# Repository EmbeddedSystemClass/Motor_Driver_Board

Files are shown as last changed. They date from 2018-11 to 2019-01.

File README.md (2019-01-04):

# ZJUNlict Motor Driver Board

The motor driver board is used to drive the motor and report the over current signal to the [mother board](https://github.com/ZJUNlict/Mother_Board). (The board is designed using [Altium Designer](https://www.altium.com/altium-designer/) 17.1)

We use half-bridge driver shown in the figure below for BLDC motors. 

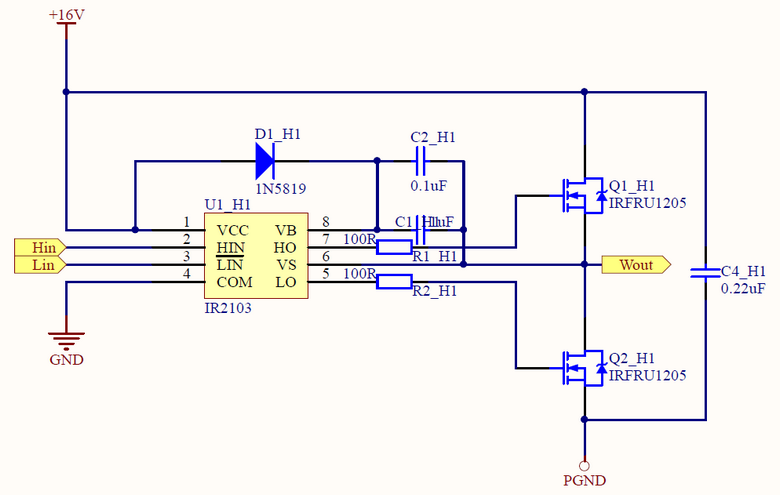
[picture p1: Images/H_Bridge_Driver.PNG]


The main features are:

* Use half-bridge driver(IR2103) to drive MOSFETs(IRFR1205) with internal set deadtime to reduce the complex of core board driver algorithm.
* Current sensor(ACS712) measures the current draw of each motor. Then the comparator(LM339) compares the output voltage signal with reference voltage to detect overcurrent scenarios.
* Motor driver boards uses modular design. One Half-bridge module handles one motor for easier fault identification and quick replacement.

The photos of the motor driver board are shown below as references. 

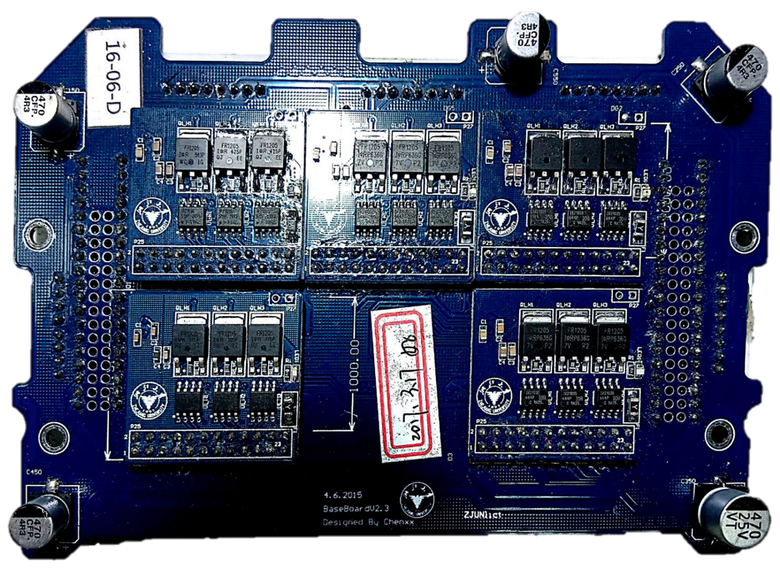
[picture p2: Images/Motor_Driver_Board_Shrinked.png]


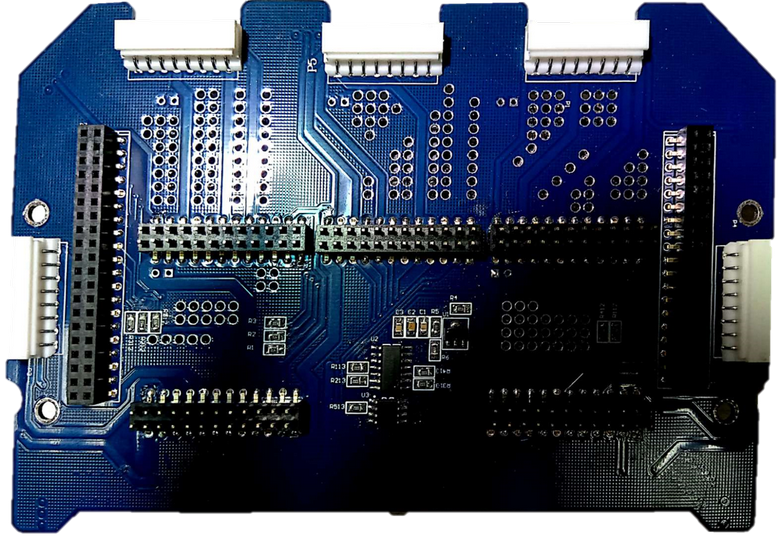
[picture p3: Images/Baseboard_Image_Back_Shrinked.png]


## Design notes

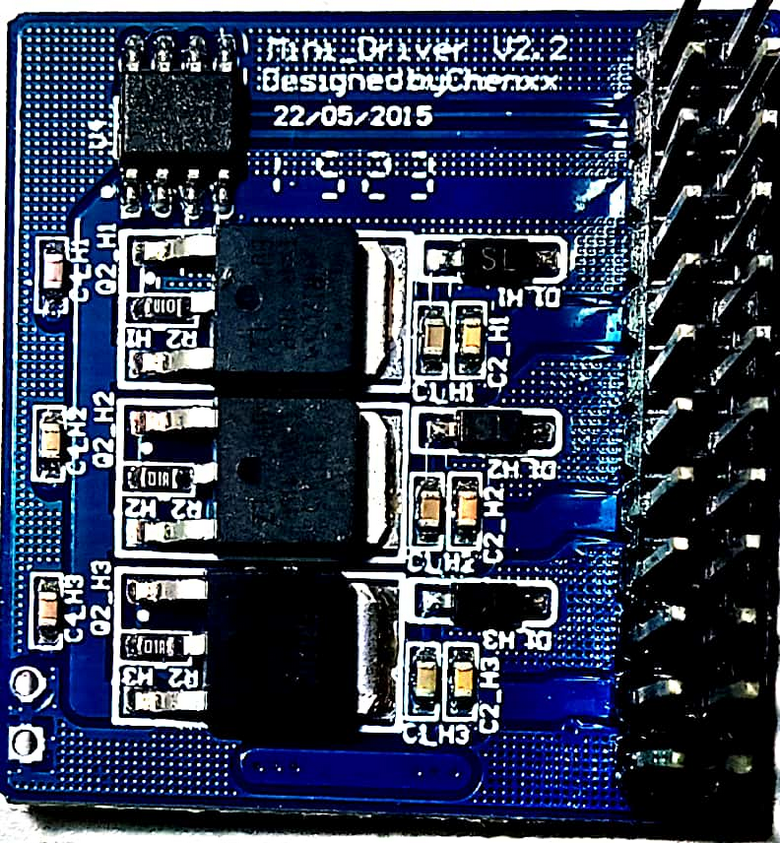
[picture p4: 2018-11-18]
Images/HBridge_Image_Back_Shrinked.png

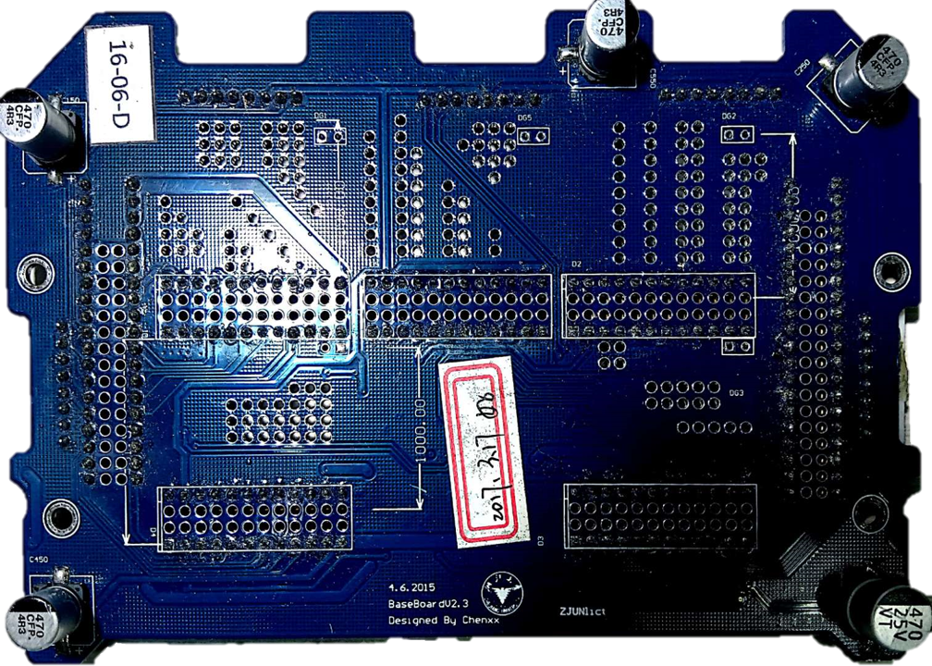
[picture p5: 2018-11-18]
Images/Baseboard_Image_Front.png

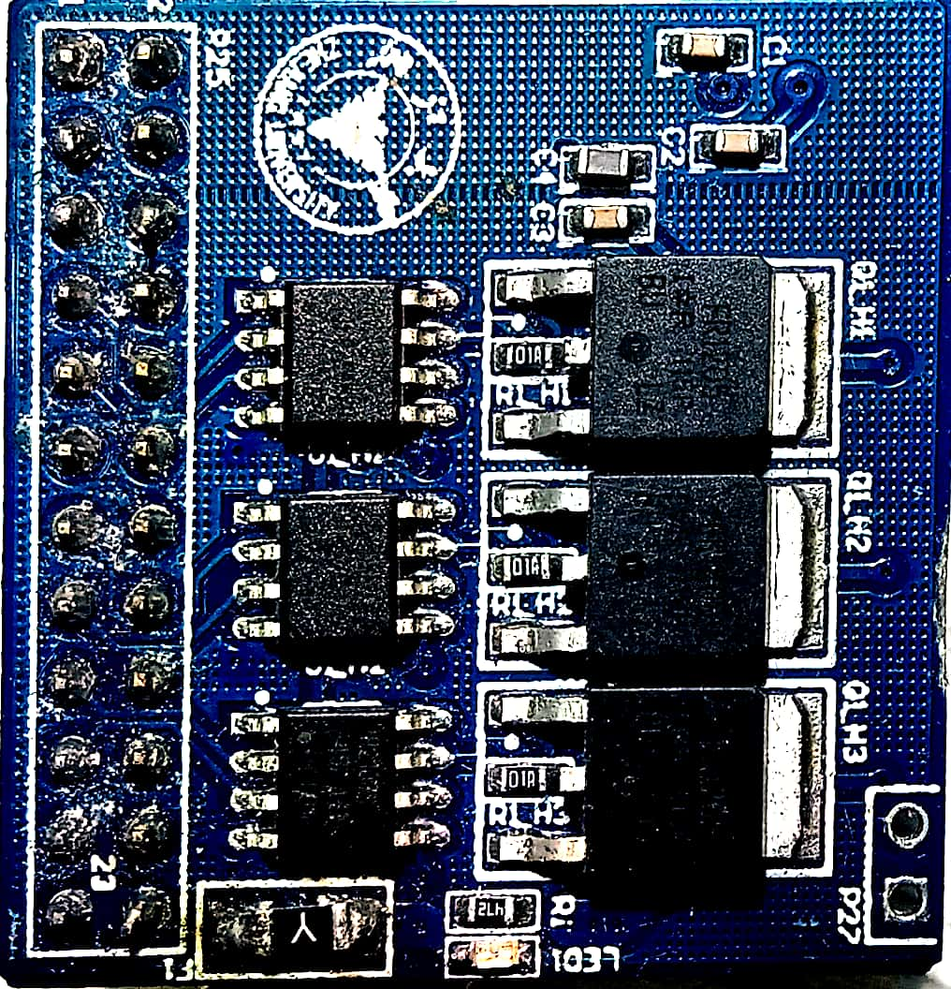
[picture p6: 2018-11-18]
Images/HBridge_Image_Front.png

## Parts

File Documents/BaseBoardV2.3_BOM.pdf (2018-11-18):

Comment | Description | Designator | Footprint | LibRef | Quantity
0.1uF | | C1, C3 | 0805 | cap | 2
1uF | | C2 | 0805 | cap | 1
470uF | 470uF | C150, C250, C350, C450, C550 | Cap - duplicate1 | cap-pol | 5
header-12X2 | | D1, D2, D3, D4, D5 | Header-12X2-wgj | NDK-22P | 5
Header 2 | | DG1, DG2, DG3, DG4, DG5 | HDR1X2 | header-2P | 5
BNC | BNC Elbow Connector | H1, H2, H3, H4 | BNC | BNC | 4
Header_8P | Header, 8-Pin | P1, P2, P3, P4, P5 | Header_8P | Header 8 | 5
Header_19*2P | Header, 19-Pin, Dual row | P6 | Header_19*2P | Header 19X2 | 1
Header_20*2P | | P7 | Header_20*2P | Header_20*2P | 1
4.7K | | R1, R2, R3 | 0805 | res | 3
470 | | R4 | 0805 | res | 1
1.6k | | R5 | 0805 | res | 1
22k | | R6 | 0805 | res | 1
10K | | R112, R113, R212, R213, R312, R313, R412, R413, R512, R513 | 0805 | res | 10
TL431CLP | | U1 | SOT89 | TL431CLP | 1
LM339 | | U2 | SOP14 | LM339 | 1
LM393 | | U3 | LM393 | LM393 | 1

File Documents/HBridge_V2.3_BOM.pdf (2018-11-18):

Bill of Materials | Bill of Materials For PCB Document [HBridge_V2.3.PcbDoc]
Source Data From: | HBridge_V2.3.PcbDoc
Project: | | H-Bridge-SingleV2.2.PrjPCB
Variant: | | None
Creation Date: 2015/6/4 | 22:10:00
Print Date: | 43422 | 43422.83022
Footprint | Comment | LibRef | Designator | Description | Quantity
0603 | 1nF | cap | C1 | | 1
0603 | 1uF | cap | C1_H1, C1_H2, C1_H3 | | 3
0603 | 0.1uF | cap | C2, C2_H1, C2_H2, C2_H3, C3 | | 5
0603 | 10uF | cap | C4 | | 1
0603 | 0.22uF | cap | C4_H1, C4_H2, C4_H3 | | 3
SOD-123 | 1N5819 | diode | D1_H1, D1_H2, D1_H3 | | 3
FUSE | 5A | FUSE | F1 | | 1
0603_diode | green | led | LED1 | | 1
HDR2X12 | Header 12X2 | Header 12X2 | P25 | Header, 12-Pin, Dual row | 1
HDR1X2 | Header 2 | Header 2 | P27 | Header, 2-Pin | 1
TO-252 | IRFRU1205 | IRFRU1205 | Q1_H1, Q1_H2, Q1_H3, Q2_H1, Q2_H2, Q2_H3 | | 6
0603 | 4.7k | res | R1 | | 1
0603 | 100R | res | R1_H1, R1_H2, R1_H3, R2_H1, R2_H2, R2_H3 | | 6
SOIC-8 | IR2103 | IR2103 | U1_H1, U1_H2, U1_H3 | | 3
SOIC-8 | ACS712 | ACS712 | U4 | | 1
| | | | | 37
Approved | | Notes
Altium Limited Confidential | 2018/11/18 | Page 1

### Project Full Path Project Filename Variant Name Data-Source Filename Data-Source Full Path Title Total Quantity Report Time Report Date Report Date & Tine Output Name Output Type Output Generator Name Output Generator Description

D:\Engneering\electronics\project\ZJUNlict_Brushless\HBridge-V2.2\H-Bridge-SingleV2.2.PrjPCB H-Bridge-SingleV2.2.PrjPCB
None
HBridge_V2.3.PcbDoc
D:\Engneering\electronics\project\ZJUNlict_Brushless\HBridge-V2.2\HBridge_V2.3.PcbDoc Bill of Materials For PCB Document [HBridge_V2.3.PcbDoc]
37
22:10:00
2015/6/4
2015/6/4 22:10:00
Bill of Materials
BOM_PartType
BOM
Bill of Materials

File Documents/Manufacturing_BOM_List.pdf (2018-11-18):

Comment | Description | Designator | Footprint | LibRef | Quantity | Company
0.1uF | ±10%,50V,-55to+125℃ | C1, C3 | 0805 | cap | 2
1uF | ±10%,50V,-55to+125℃ | C2 | 0805 | cap | 1
470uF | ±10%,25V,10*10mm,-55°C to +125°C | C150, C250, C350, C450, C550 | Cap - duplicate1 | cap-pol | 5
header-12X2 | 205-2X12P-7.62 | D1, D2, D3, D4, D5 | Header-12X2-wgj | SHPEAK | 5 SHPEAK
Header 2 | 201S-1X2PG-10.0/3.0 | DG1, DG2, DG3, DG4, DG5 | HDR1X2 | | 5
BNC | | H1, H2, H3, H4 | BNC | BNC | 4
Header_8P | 5264-8AW / 22-05-7085 | P1, P2, P3, P4, P5 | Header_8P | Header 8 | 5 MOLEX
Header_19*2P | 205-2X10P-7.62 | P6 | Header_19*2P | SHPEAK | 2 SHPEAK
Header_20*2P | 205-2X10P-7.62 | P7 | Header_20*2P | SHPEAK | 2 SHPEAK
4.7K | 0.01 R1, R2, R3 | | 0805 | res | 3
470 | 0.01 R4 | | 0805 | res | 1
1.6k | 0.01 R5 | | 0805 | res | 1
22k | 0.01 R6 | | 0805 | res | 1
10K | 0.01 R112, R113, R212, R213, R312, R313, R412, R413, R512, R513 | | 0805 | res | 10
TL431CLP | | U1 | SOT89 | TL431CLP | 1 TI
LM339 | | U2 | SOP14 | LM339 | 1 TI
LM393 | | U3 | LM393 | LM393 | 1 TI

Footprint | Comment | LibRef | Designator | Company | Description | Quantity
0603 | 1nF | cap | C1 | | ±10%，50V，-55to+125℃ | 1
0603 | 1uF | cap | C1_H1, C1_H2, C1_H3 | | ±10%，50V，-55to+125℃ | 3
0603 | 0.1uF | cap | C2, C2_H1, C2_H2, | | ±10%，50V，-55to+125℃ | 5
0603 | 10uF | cap | C4 | | ±10%，50V，-55to+125℃ | 1
0603 | 0.22uF | cap | C4_H1, C4_H2, C4_H3 | | ±10%，50V，-55to+125℃ | 3
SOD-123 | 1N5819 | DIODE | D1_H1, D1_H2, D1_H3 | DIODESINC. | | 3
1206 | 5A | FUSE | F1 | BOURNS | SF-1206S50 Slow Blow | 1
0603_diode | GREEN | LED | LED1 | | | 1
HDR2X12 | Header 2X12 | Header 12X2 | P25 | | | 1
HDR1X2 | Header 2 | Header 2 | P27 | | | 1
TO-252 | IRFRU1205 | IRFRU1205 | Q1_H1, Q1_H2, Q1_H3, Q2_H1, Q2_H2, Q2_H3 | INTERNATIONA L RECTIFIER | | 6
0603 | 4.7k | res | R1 | | 1% | 1
0603 | 100R | res | R1_H1, R1_H2, R1_H3, R2_H1, R2_H2, R2_H3 | | 1% | 6
SOIC-8 | IR2103 | IR2103 | U1_H1, U1_H2, U1_H3 | INTERNATIONA L RECTIFIER | | 3
SOIC-8 | ACS712 | ACS712 | U4 | ALLEGRO MICROSYSTEM S | | 1

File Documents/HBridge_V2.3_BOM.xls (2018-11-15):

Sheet: BOM Report
Bill of Materials |  |  | Bill of Materials For PCB Document [HBridge_V2.3.PcbDoc]
Source Data From: |  | HBridge_V2.3.PcbDoc
Project: |  | H-Bridge-SingleV2.2.PrjPCB
Variant: |  | None
Creation Date: | 2015/6/4 | 22:10:00
Print Date: | 42159 | 42159.92383
Footprint | Comment | LibRef | Designator | Description | Quantity
0603 | 1nF | cap | C1 |  | 1
0603 | 1uF | cap | C1_H1, C1_H2, C1_H3 |  | 3
0603 | 0.1uF | cap | C2, C2_H1, C2_H2, C2_H3, C3 |  | 5
0603 | 10uF | cap | C4 |  | 1
0603 | 0.22uF | cap | C4_H1, C4_H2, C4_H3 |  | 3
SOD-123 | 1N5819 | diode | D1_H1, D1_H2, D1_H3 |  | 3
FUSE | 5A | FUSE | F1 |  | 1
0603_diode | green | led | LED1 |  | 1
HDR2X12 | Header 12X2 | Header 12X2 | P25 | Header, 12-Pin, Dual row | 1
HDR1X2 | Header 2 | Header 2 | P27 | Header, 2-Pin | 1
TO-252 | IRFRU1205 | IRFRU1205 | Q1_H1, Q1_H2, Q1_H3, Q2_H1, Q2_H2, Q2_H3 |  | 6
0603 | 4.7k | res | R1 |  | 1
0603 | 100R | res | R1_H1, R1_H2, R1_H3, R2_H1, R2_H2, R2_H3 |  | 6
SOIC-8 | IR2103 | IR2103 | U1_H1, U1_H2, U1_H3 |  | 3
SOIC-8 | ACS712 | ACS712 | U4 |  | 1
 |  |  |  |  | 37
Approved |  | Notes

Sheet: Project Information
Project Full Path | D:\Engneering\electronics\project\ZJUNlict_Brushless\HBridge-V2.2\H-Bridge-SingleV2.2.PrjPCB
Project Filename | H-Bridge-SingleV2.2.PrjPCB
Variant Name | None
Data-Source Filename | HBridge_V2.3.PcbDoc
Data-Source Full Path | D:\Engneering\electronics\project\ZJUNlict_Brushless\HBridge-V2.2\HBridge_V2.3.PcbDoc
Title | Bill of Materials For PCB Document [HBridge_V2.3.PcbDoc]
Total Quantity | 37
Report Time | 22:10:00
Report Date | 2015/6/4
Report Date & Tine | 2015/6/4 22:10:00
Output Name | Bill of Materials
Output Type | BOM_PartType
Output Generator Name | BOM
Output Generator Description | Bill of Materials

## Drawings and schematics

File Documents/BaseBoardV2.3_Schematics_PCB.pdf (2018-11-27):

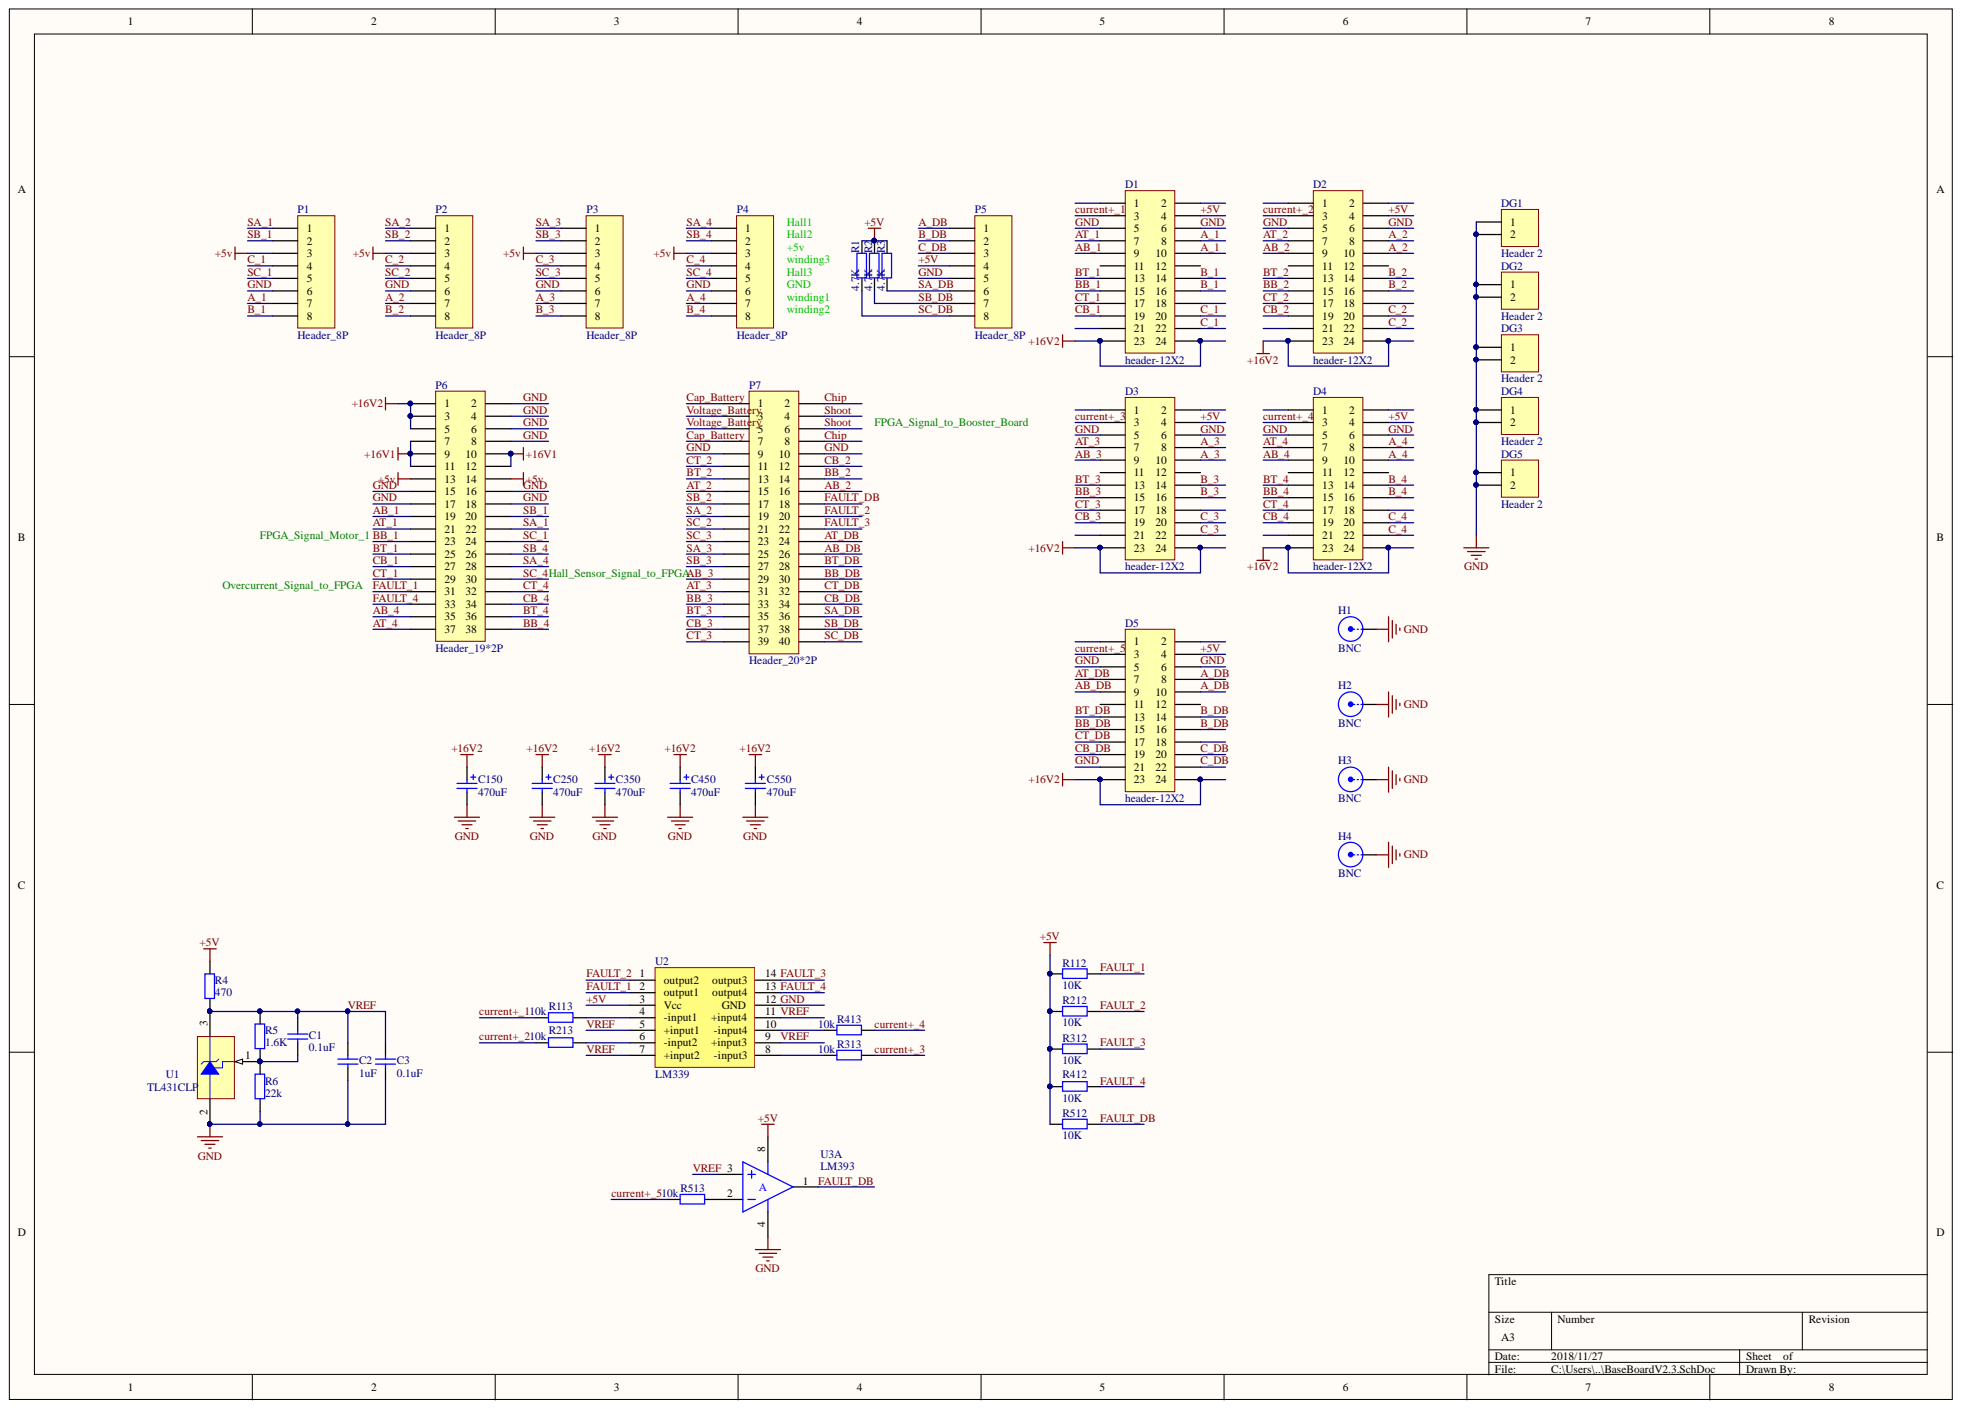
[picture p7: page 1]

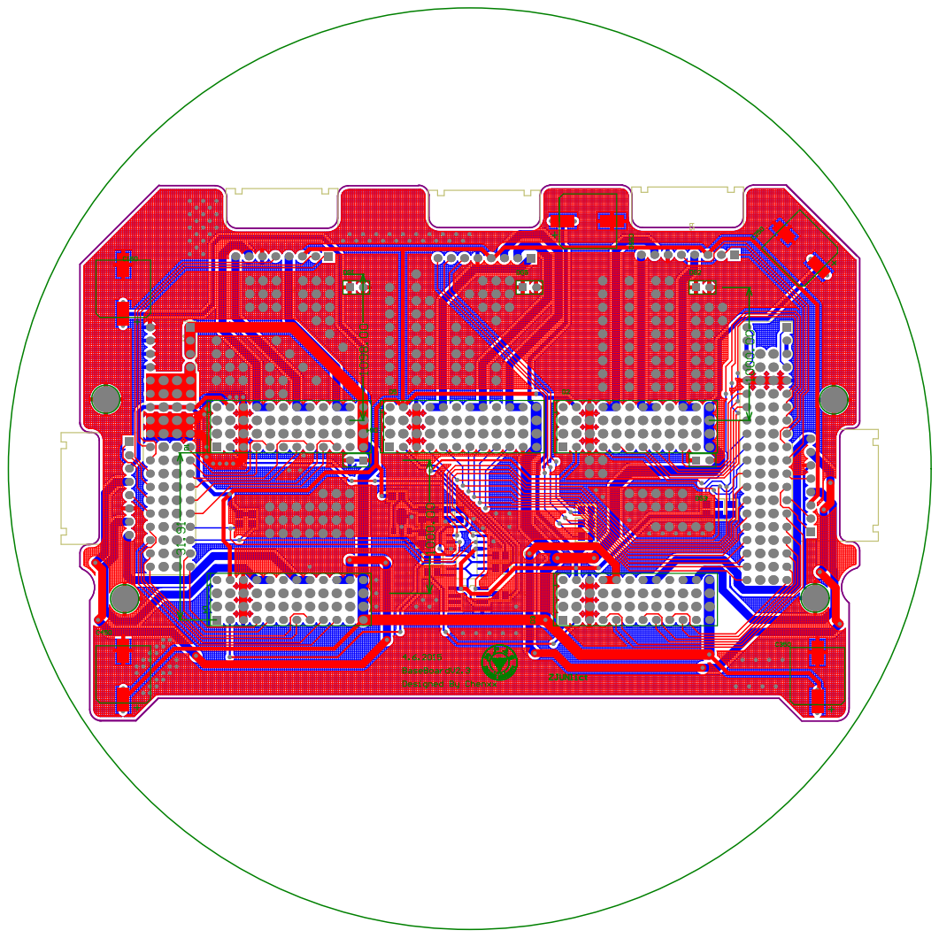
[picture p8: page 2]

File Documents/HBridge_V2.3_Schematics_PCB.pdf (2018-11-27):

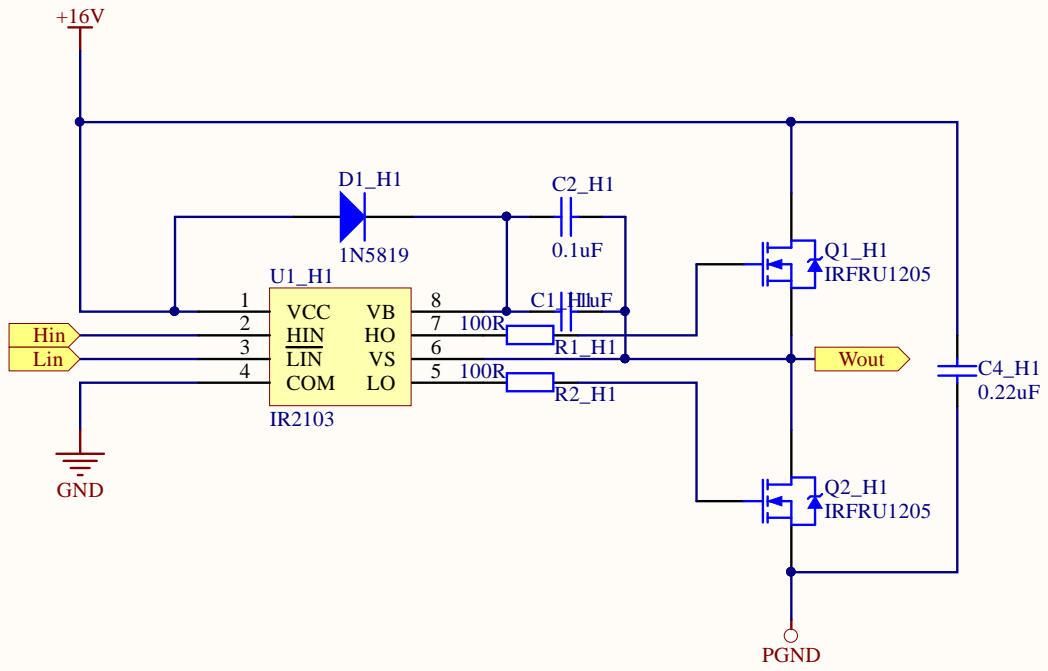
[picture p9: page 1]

7 1 0
6 | R1 _ H 1

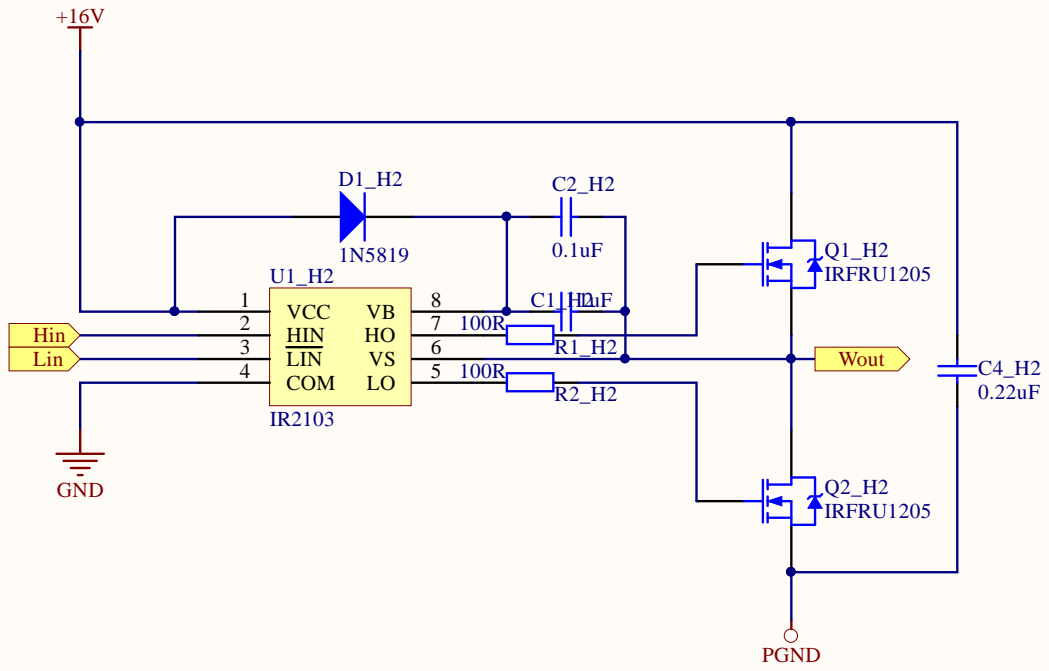
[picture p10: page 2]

7 1 0
6 | R1 _ H 2

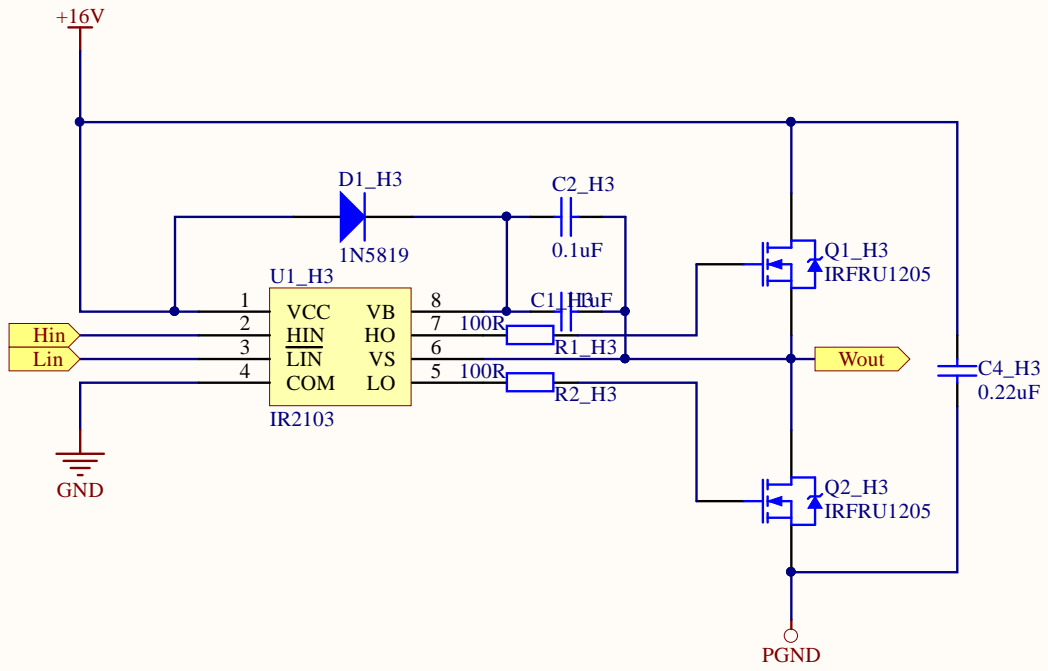
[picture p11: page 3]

7 1 0
6 | R1 _ H 3

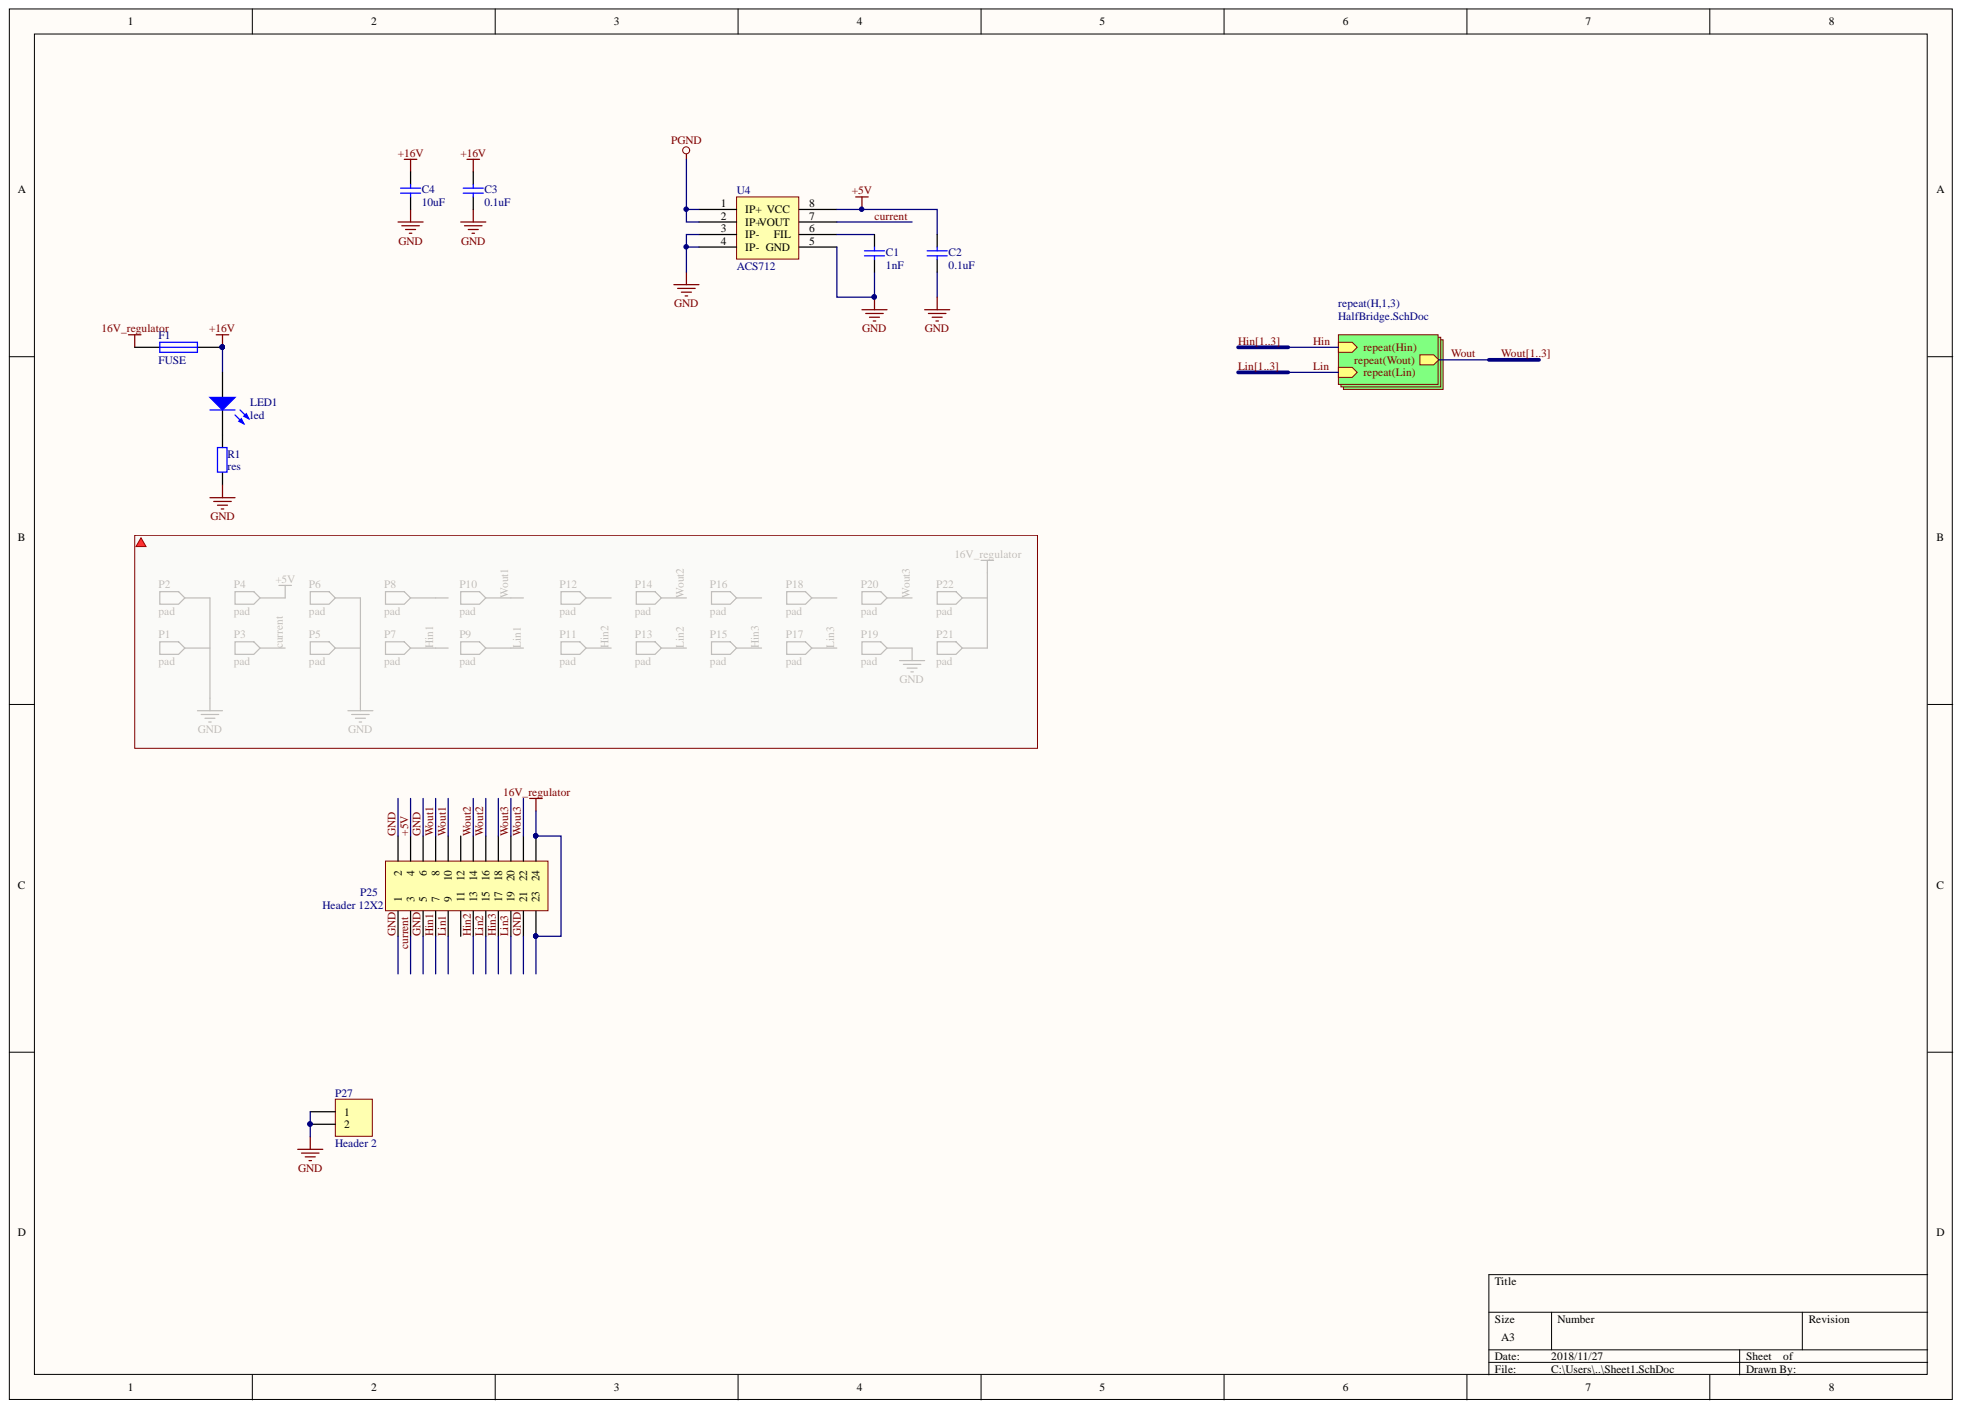
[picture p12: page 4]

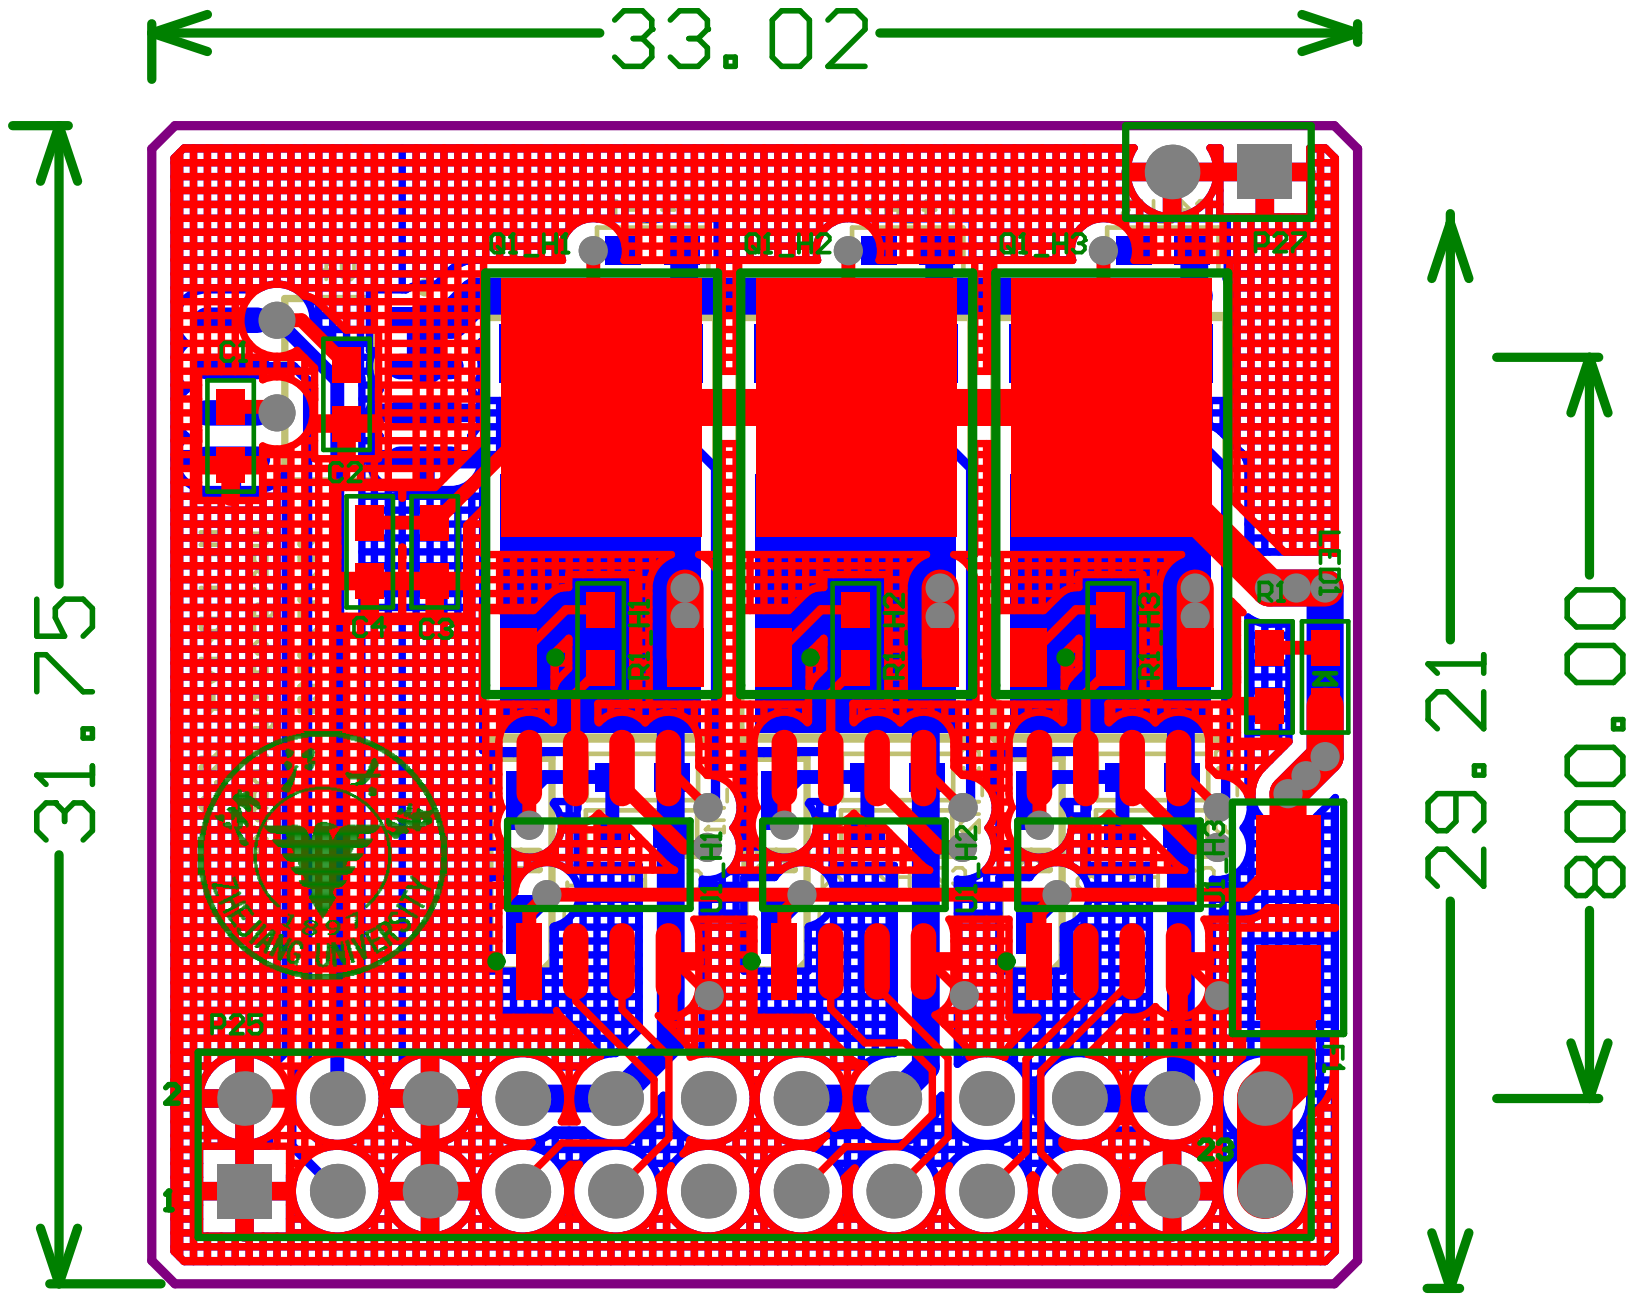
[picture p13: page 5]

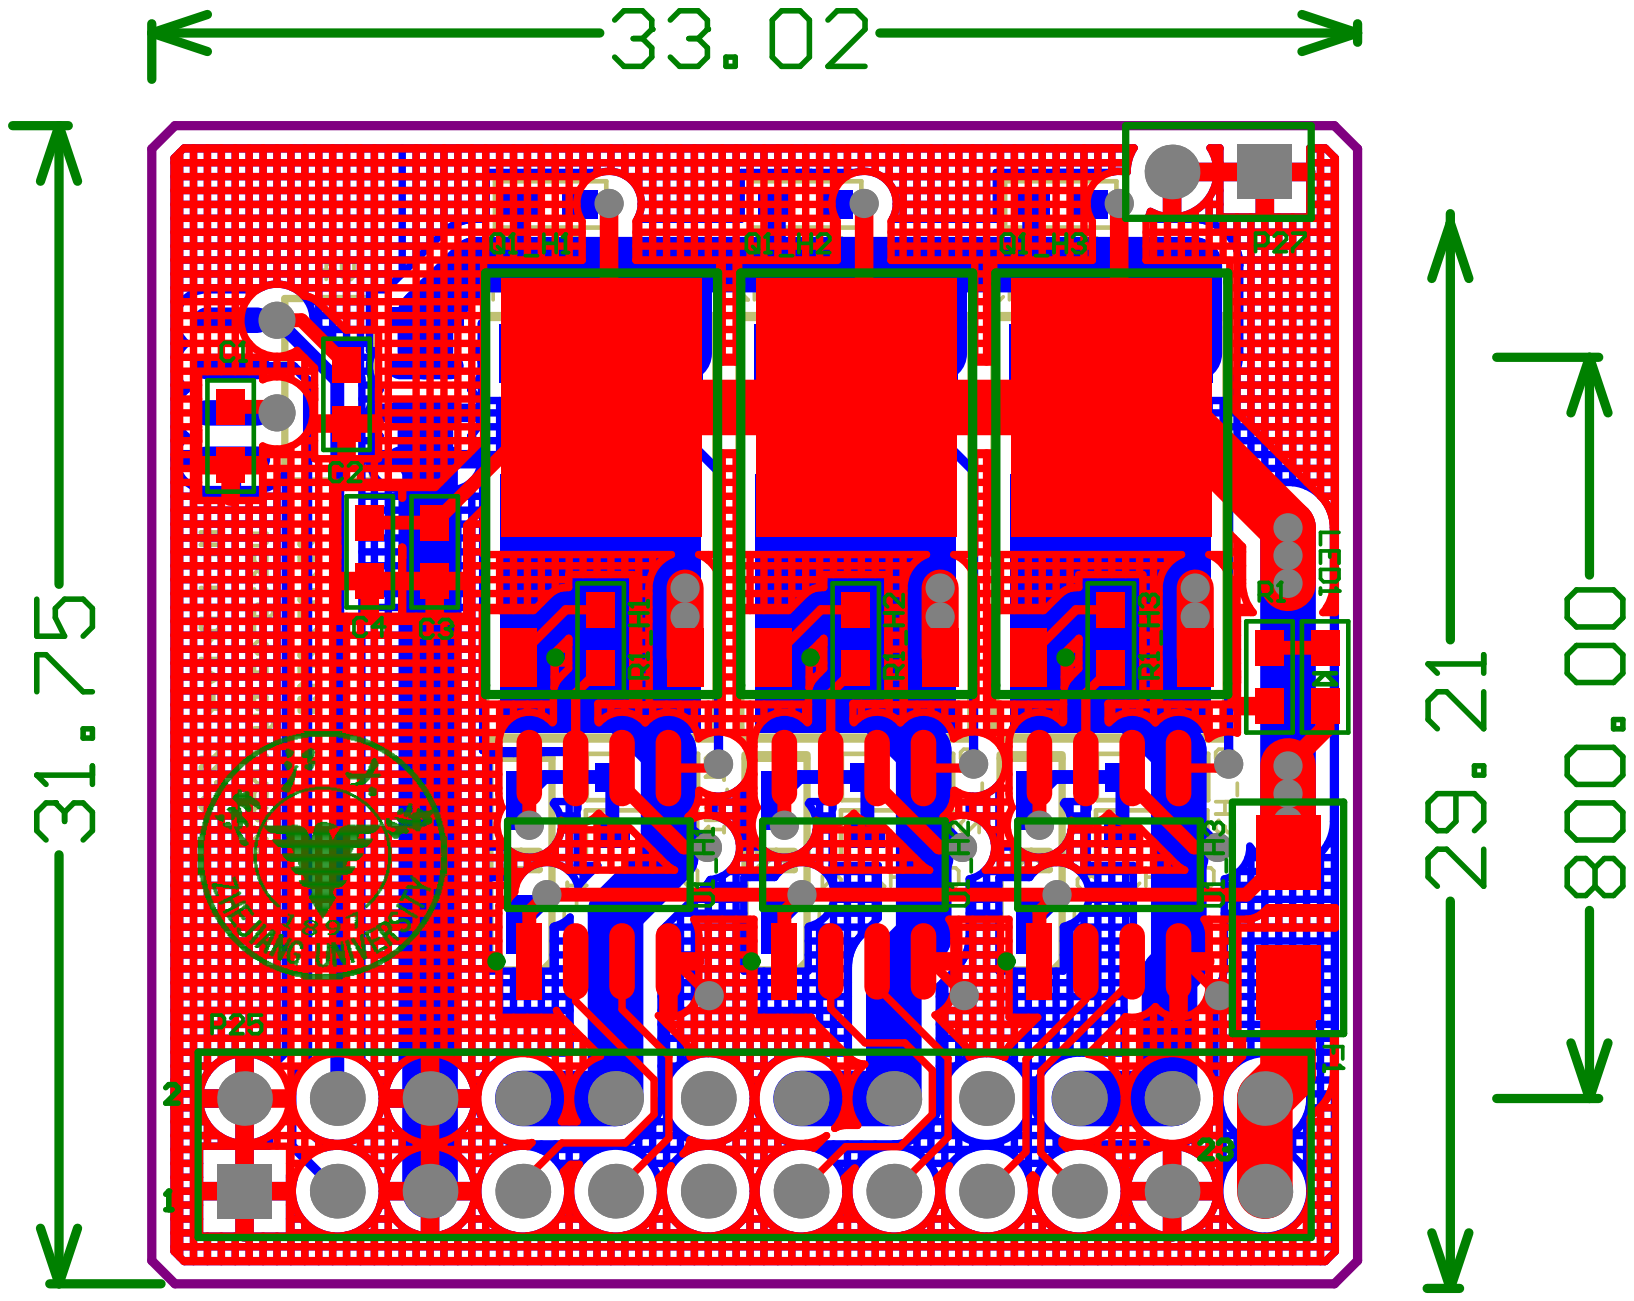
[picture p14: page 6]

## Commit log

2018-11-15 Add base board and hbridge board PCB designs
    [BaseBoardV2.3.PcbDoc, BaseBoardV2.3.PrjPCB, BaseBoardV2.3.SchDoc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]
2018-11-18 Add documents and images
    [BaseBoardV2.3_BOM.xls, HBridge_V2.3_BOM.xls, Manufacturing_BOM_List.xls]
2018-11-27 Add Schematics and PCB pdfs
2018-11-28 Add driver board readme
2019-01-04 Move excel files
    [BaseBoardV2.3.PrjPCB]
